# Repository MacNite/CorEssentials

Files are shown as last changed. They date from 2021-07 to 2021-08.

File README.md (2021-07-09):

# CorEssentials MK1
CorEssentials is an open source corexy 3D printer. This printer combines the best of the most popular 3D printers:

Voron V1.8 / V2.4 by VoronDesign: https://vorondesign.com/

HevoRT https://hevort.com/

Railcore https://railcore.org/

VZBot https://grabcad.com/library/vzbot-1

# supported by https://www.cr-3d.de

- Built Volume: 310 mm x 310 x mm x 310 mm
- Frame: Built from 2040, 2020 and 3030 Aluminium Extrusion
- Hotend: Trianglelab Dragon (0.4mm)
- Extruder: CR3D NanoXtruder
- Bed Leveling: Hardware bed leveling with 2 independent motors
- Built Plate: Magnetic Spring Steel with PEI or Pertinax
- Heated Bed: 230V, 800W silicone heater up to 120°C
- Connectivity: 7" Touchscreen, Wifi
- Filament runout sensor (Prusa Mini)
- Enclosure: Completely enclosed print volume with active temperature regulation and passive heated chamber (through heated bed)
- LED illumination
- Open for all Filament
- Filament Diameter: 1.75mm
- Supported Filament: ABS, ASA, PC, Nylon, PETG, PLA, PP, HIPS and much more // carbon and particle filled filaments possible with different toolhead
- Controller: Duet Mini 5+
- Power Supply: Meanwell 24V 10A, second PSU for High Voltage Stepper Drivers possible
- Coldend cooling: 3010 axial fan
- Part cooling: 1x 4020 blower fan
- Chamber fan & filtration: 6010 blower fan
- Electronics cooling: 2x 6015 axial fan
- Linear Motion: CE MGN9H for xy gantry and 8mm rods for z
- Completely open source: all Fusion 360 files and .stp assembly available

Find the Fusion360 model for your viewing/download pleasure here (you can download the F360 model through this link as well):

https://a360.co/3fYgmHP

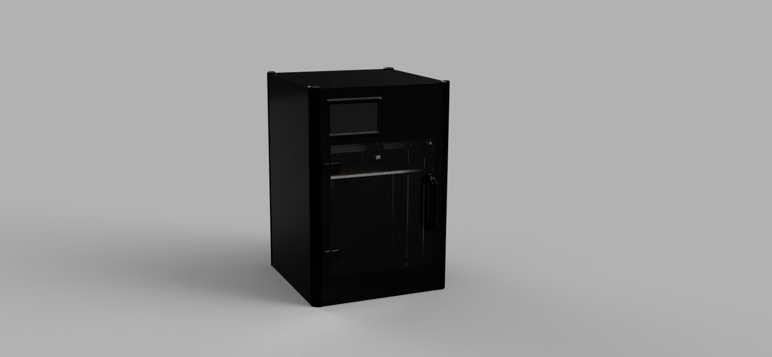
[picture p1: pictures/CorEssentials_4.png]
CorEssentials MK1


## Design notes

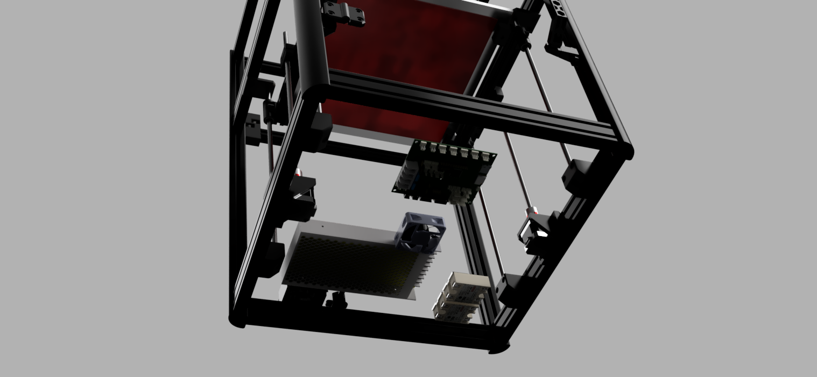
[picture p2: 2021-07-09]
pictures/CorEssentials_3.png

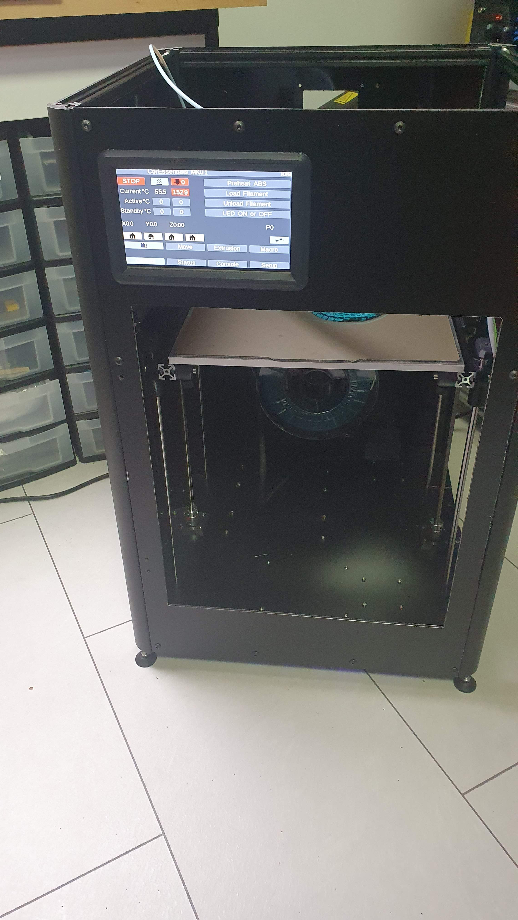
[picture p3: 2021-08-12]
pictures/CorEssentials_MK01_Foto1.jpg

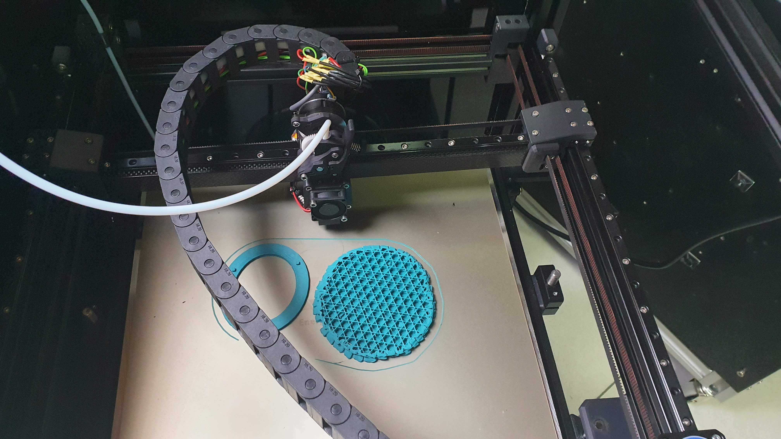
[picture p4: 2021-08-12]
pictures/CorEssentials_MK01_Foto3.jpg

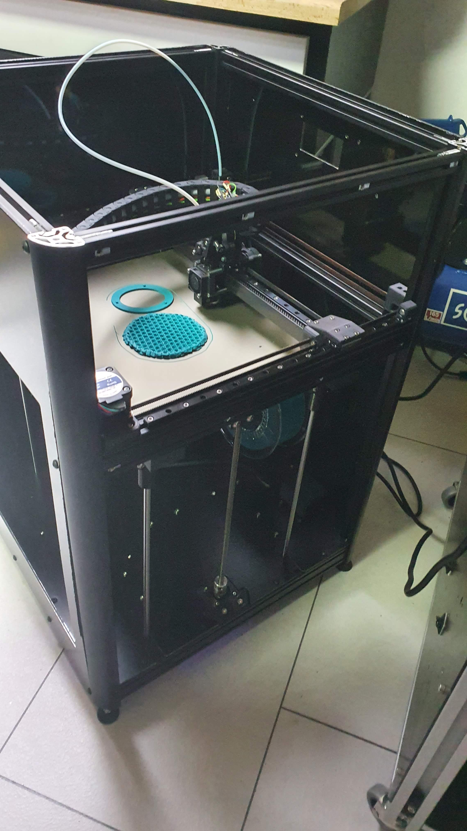
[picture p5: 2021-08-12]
pictures/CorEssentials_MK01_Foto2.jpg

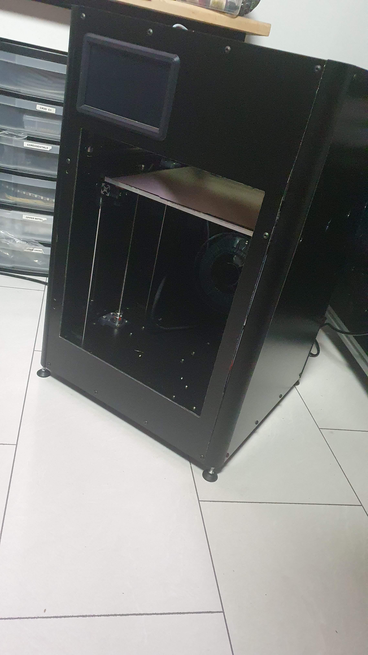
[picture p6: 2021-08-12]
pictures/CorEssentials_MK01_Foto4.jpg

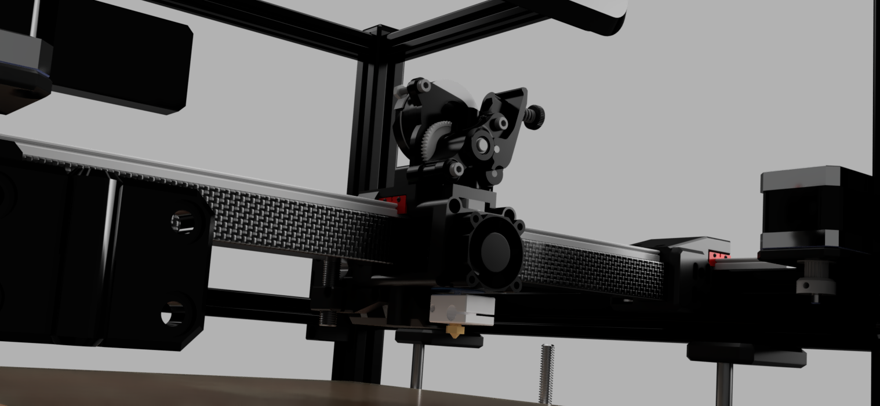
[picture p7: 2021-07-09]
pictures/CorEssentials_2.png

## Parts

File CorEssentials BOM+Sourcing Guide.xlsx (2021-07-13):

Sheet: Configurator
Configurator
Attention: The files for the panels are only available for the standard 310 x 310 x 310 mm³ built volume. If you plan to built any other size you have to edit the panels yourself.
Fields with this colour are input fields
Fields with this colour are name / title fields
Filds with this colour have formulas in them
Built Volume
Travel in x | 310 | mm
Travel in y | 310 | mm
Travel in z | 310 | mm
Fully enclosed? | yes
Corner Connection? | automatic connectors (more expensive but cleaner)
Needed Aluminium Profiles
Profile | Length |  | Amount needed | Used for
2020 | 410 | mm | 2 | Frame x
2020 | 420 | mm | 2 | Frame y
2020 | 351 | mm | 1 | Frame Back
4020 | 410 | mm | 2 | Frame x
4020 | 420 | mm | 4 | Frame y
3030 | 681 | mm | 4 | Frame z
2020 | 284 | mm | 2 | Bed Carrier
Carbon 20x20 |  | mm | 1 | x-Axis
Needed Linear Motion Components
Type | Length |  | Amount needed | Used for
8mm Rod | 404 | mm | 4 | z Axis
TR8x1,5 | 365 | mm | 2 | z Axis
MGN9H | 350 | mm | 1 | x Axis
MGN9H | 350 | mm | 2 | y-Axis
Built Plate
Component | Length |  | Amount needed | Used for
Bed Plate t = 8mm | 320 | mm | 1 | x-Length
 | 320 | mm |  | y-Length
Silicone Heater | 280 | mm | 1 | x-Length
 | 280 | mm |  | y-Length
Springsteel Sheet | 310 | mm | 1 | x-Length
 | 310 | mm |  | y-Length
Panels for enlcosure
Component | Length |  | Amount needed | Used for
Front + Back | 410 | mm | 2 | x-Length
 | 681 | mm |  | z-Length
Left+Right | 420 | mm | 2 | y-Length
 | 681 | mm |  | z-Length
Inner, Top, Bottom | 460 | mm | 3 | x-Length
 | 470 | mm |  | y-Length

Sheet: CorEssentials BOM
Category | Component | QTY | approx. Price | Source (partially affiliate links) | Note / Alternative Source
Filament | ABS Filament, 1kg | 1 | 25.00 €
Frame | 2020, L= 410mm | 2 | 135.00 € | https://www.myaluprofil.de/advanced_search_result.php?categories_id=0&inc_subcat=1 | Frame x
Frame | 2020, L= 420mm | 2 |  |  | Frame y
Frame | 2020, L= 351mm | 1 |  |  | Frame Back
Frame | 4020, L= 410mm | 2 |  | https://www.myaluprofil.de/Aluminiumprofil-20x40-Nut-5--I-Typ-.html | Frame x
Frame | 4020, L= 420mm | 4 |  |  | Frame y
Frame | 3030, L= 681mm | 4 |  | https://www.myaluprofil.de/Aluminiumprofil-R30x90---Nut-6--I-Typ-leicht-.html | Frame z
Frame | 2020, L= 284mm | 2 |  | https://www.myaluprofil.de/advanced_search_result.php?categories_id=0&inc_subcat=1 | Bed Carrier
Frame | Carbon 20x20, L= mm | 1 | 18.00 € | https://s.click.aliexpress.com/e/_AAvO8Y | 20x20x18
Frame | Automatic Connector | 50 | 82.00 € | https://www.myaluprofil.de/gewinde-formverbindersatz-nut-5-i-typ.html
Fasteners | M5 Thumbscrews for Bed | 4 | 4.00 € | https://s.click.aliexpress.com/e/_AW3sgC
Fasteners | M3 Nyloc Nut | 25 | 2.00 € | https://s.click.aliexpress.com/e/_AEa5uM
Fasteners | M4 Nyloc Nut | 4 | 100.00 €
Fasteners | BHCS M3x20 | 4
Fasteners | BHCS M3x30 | 4
Fasteners | BHCS M3x35 | 4
Fasteners | BHCS M3x40 | 4
Fasteners | BHCS M4x6 | 8
Fasteners | BHCS M4x14 | 4
Fasteners | BHCS M5x8 Black | 83
Fasteners | BHCS M5x10 | 9
Fasteners | BHCS M5x12 | 6
Fasteners | BHCS M5x20 | 10
Fasteners | BHCS M5x25 | 3
Fasteners | BHCS M5x35 | 2
Fasteners | SHCS M2.5x8 | 4
Fasteners | SHCS M3x8 | 29
Fasteners | SHCS M3x10 | 12
Fasteners | SHCS M3x12 | 4
Fasteners | SHCS M3x16 | 1
Fasteners | SHCS M3x18 | 3
Fasteners | SHCS M3x20 | 10
Fasteners | SHCS M3x25 | 5
Fasteners | SHCS M3x35 | 3
Fasteners | SHCS M3x50 | 2
Fasteners | SHCS M5x30 | 6
Fasteners | T-Slot Nut, Slot 5, M3 | 11
Fasteners | T-Slot Nut, Slot 5, M5 | 106
Fasteners | T-Slot Nut, Slot 6, M4 | 50
Fasteners | T-Slot Nut, Slot 6, M5 | 9
Fasteners | Countersunk M3x8 | 8
Fasteners | Countersunk M5x25 | 4 |  |  | Bed
Motion | 8mm Rod, L= 404mm | 4 | 16.00 € | https://de.aliexpress.com/item/32676553191.html | z Axis
Motion | TR8x1,5, L= 365mm | 2 | 12.00 € | https://www.motedis.com/shop/Dynamik/Trapezgewindespindel-Zubehoer/Trapezgewindespindel-RPTS-rechts-TR-16x4-L%3D1000mm::4800.html | z Axis
Motion | MGN9H, L= 350mm | 1 | 14.00 € | https://de.aliexpress.com/item/33043386369.html?spm=2114.13010708.0.0.9a244c4dHEINjY | x Axis
Motion | MGN9H, L= 350mm | 2 | 28.00 € | https://de.aliexpress.com/item/33043386369.html?spm=2114.13010708.0.0.9a244c4dHEINjY | y-Axis
Motion | Coupling 8x5mm - Leadscrew to stepper | 2 | 15.00 € | https://de.aliexpress.com/item/32673106538.html?spm=2114.13010708.0.0.14d84c4dMCanQh
Motion | TR8x1,5 Leadscrew Nut (IGUS) | 1 | 8.00 € | https://www.motedis.com/shop/Dynamik/Trapezgewindespindel-Zubehoer/Standard-Anti-backlash-Delrin-Mutter-TR-8x15::3955.html
Motion | GT2 6mm Belt, 4m | 1 | 18.00 € | https://s.click.aliexpress.com/e/_AEHEpa
Motion | GT2 16T Idler - Smooth / no teeth - Bore 3mm | 2 | 6.00 € | https://s.click.aliexpress.com/e/_A8v4QU
Motion | GT2 16T Idler - with teeth - Bore 3mm | 6 | 16.00 € | https://s.click.aliexpress.com/e/_A8v4QU
Motion | GT2 20T Pulley - Bore 5mm | 2 | 5.00 € | https://s.click.aliexpress.com/e/_Aerhni
Motion | LM8UU | 8 | 7.00 € | https://de.aliexpress.com/item/32227295989.html
Electronics | Triangelalab Dragon Hotend (High Flow) | 1 | 70.00 € | https://s.click.aliexpress.com/e/_AFV3Is
Electronics | Trianglelab 50Watt Heater Cartridge, 24V | 1 | 3.00 € | https://s.click.aliexpress.com/e/_A3MKFA
Electronics | Termistor 104GT-2 104 NT | 2 | 8.00 € | https://s.click.aliexpress.com/e/_Alchb2
Electronics | Prusa Mini Filament Sensor Electronics | 1 | 8.00 € | https://s.click.aliexpress.com/e/_AXDKUC
Electronics | 3010 axial fan, Dual Ball Bearing, 24V | 1 | 11.00 € | https://s.click.aliexpress.com/e/_9jQWYg
Electronics | 6010 axial fan, Dual Ball Bearing, 24V | 2 | 9.00 € | https://s.click.aliexpress.com/e/_AK0dze
Electronics | 6015 Blower Fan, Dual Ball Bearing, 24V | 1 | 8.00 € | https://s.click.aliexpress.com/e/_9HHvkM
Electronics | 4020 blower fan, Dual Ball Bearing, 24V | 1 | 9.00 € | https://s.click.aliexpress.com/e/_9GZzKu
Electronics | Fysetc PanleDue 7i | 1 | 50.00 € | https://s.click.aliexpress.com/e/_AfTH3w
Electronics | Fysetc Duet 3 Mini 5+ Wifi | 1 | 55.00 € | https://s.click.aliexpress.com/e/_9QsNAY | https://www.cr3d.de/produkt/duet-3-mini-5/
Electronics | CR3D SupCRprobe 8mm kurz (Alternative: Prusa SuperPinda) | 1 | 25.00 € | https://www.cr3d.de/produkt/supcrprobe-8mm-kurz/
Electronics | Wifi Antenna cable extension (SMA Female 100cm) | 1 | 3.00 € | https://s.click.aliexpress.com/e/_9w3PT2
Electronics | Nema 17 (Body L<40mm), 17HS19-2004S1 | 4 | 40.00 € | https://s.click.aliexpress.com/e/_9yAVtA
Electronics | SSR for Heated Bed (current rating at least 10A AC) | 1 | 30.00 € | https://www.cr3d.de/produkt/solid-state-relais-10a/
Electronics | Thermal Fuse for Heated Bed, 125°C | 1 | 3.00 € | https://s.click.aliexpress.com/e/_9Ah1FE
Electronics | IEC Socket with fuse and switch (Type AC-17) | 1 | 5.00 € | https://s.click.aliexpress.com/e/_Apvyuo
Bed | Bed Plate t = 8mm, 320x320mm | 1 | 42.00 € | https://www.metall-kunststoffhandel.de/produkt/aluminium-al-mg-45-mn-8-mm-feinstgefraest/
Bed | Silicone Heater, 280x280mm | 1 | 20.00 € | https://s.click.aliexpress.com/e/_ArIUe8
Bed | Springsteel Sheet, 310x310mm | 1 | 37.00 € | https://s.click.aliexpress.com/e/_9HHdEY
Other | CR3D NanoXTruder (Alternative: Print parts on your own and buy Orbiter) | 1 | 70.00 € | https://www.cr3d.de/produkt/cr-3d-nanoxtruder/ | https://de.aliexpress.com/item/1005002487727392.html?spm=2114.13010708.0.0.3a994c4dKlcmqN
Other | Front + Back, 410x681mm, thickness: 3 to 4 mm | 2 | 150.00 € | https://kunststoffplattenonline.de/product/alupanel-alu-verbundplatten-schwarz-3-mm/ | a) can be cnc / cut with hand tools from aluminium composite panel b) can be hand cut (knife) from PVC foam or similar c) can be ordered form laser-cutting services in 3mm aluminium
Other | Left+Right, 420x681mm, thickness: 3 to 4 mm | 2
Other | Inner, Top, Bottom, 460x470mm, thickness: 3 to 4 mm | 3
Other | Filter for Enclosure | 1 | 5.00 € | https://s.click.aliexpress.com/e/_ABCy64
Sum |  |  | 1172.00 €

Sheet: Fusion360_BOM_Import
Parts List
Qty | Part Number | ITEM Slot 6 Nut M4
 |  | 0
1 | AC_Power_Socket-3_pin_250V_10A_AC-17
1 | Case_PC
2 | Êîíòàêò
1 | Êîíòàêò_GND
3 | Êëåéìà
1 | Fuse_contact
1 | Êîíòàêò_fuse
1 | Fuse_holder
1 | Fuse_contact (1)
1 | Êîíòàêò_fuse
1 | Fuse_holder
1 | Ïåðåìû÷êà
1 | SWITCH KCD1-104_Default<As Machined>
1 | Äåðæàòåëü_ïðåäîõðàíèòåëÿ_ñ_ïðåäîõðàíèòåëåì
1 | Äåðæàòåëü_ïðåäîõðàíèòåëÿ
1 | Fuse Small 1A
3 | CornerConnector
1 | M5 Threaded Insert
1 | 92095A208_Button Head Hex Drive Screw
1 | IEC_Cover
1 | Chamber_Fan_Cover
2 | 60mm Fan
1 | Fan_Case
1 | Fan
2 | Meanwell LRS-200-24
1 | Duet3_5+_Wifi
1 | USB_Micro-B_Molex_47346-0001
1 | SOLID
1 | IDC-Header_2x13_P2.54mm_Vertical
1 | SOLID (5)
1 | 9.5mm_1x4
1 | SOLID (7)
7 | Molex_KK-254_AE-6410-02A_1x02_P2.54mm_Vertical
1 | SOLID (11)
3 | IDC-Header_2x05_P2.54mm_Vertical
1 | SOLID (13)
1 | 693071020811_Download_STEP_693071020811_rev1
1 | COMPOUND (1)
1 | ESP-WROOM-02U
1 | SOLID (15)
3 | PinHeader_1x03_P2.54mm_Vertical
1 | SOLID (17)
5 | Molex_KK-254_AE-6410-03A_1x03_P2.54mm_Vertical
1 | SOLID (20)
1 | PinHeader_1x16_P2.54mm_Vertical
1 | SOLID (21)
7 | Molex_KK-254_AE-6410-04A_1x04_P2.54mm_Vertical
1 | SOLID (25)
1 | PinHeader_2x05_P2.54mm_Vertical
1 | SOLID (27)
1 | TQFP-128_14x14mm_P0.4mm
1 | SOLID (30)
1 | C-K_Components_Switch_Tactile_KMS
1 | COMPOUND (4)
1 | PinHeader_1x02_P2.54mm_Vertical
1 | SOLID (38)
5 | Molex_KK-254_AE-6410-05A_1x05_P2.54mm_Vertical
1 | SOLID (39)
2 | B2P-VH-B-white
1 | SOLID (40)
2 | Mini_Blade_Fuse_Holder
1 | COMPOUND (5)
2 | Fuse_MINI
1 | COMPOUND (6)
1 | COMPOUND (7)
4 | DoorHinge
1 | DoorHandle
1 | Door_Lock_C
2 | Door_Lock_A
1 | 92095A210_Button Head Hex Drive Screw
1 | Door_Lock_B
1 | DasFilament_Standard
1 | Prusa_Mini FilamentSensor
1 | MINI-fsenzor-lever
1 | MINI-fsenzor-cover
1 | MINI-fsenzor-box
1 | 90751A113
1 | 92095A214_Button Head Hex Drive Screw
1 | 90128A205
1 | 91274A103
1 | Spool_Holder
1 | Bowden_Tube_Clip
8 | Magnet_6x3mm
10 | M3 Threaded Insert
1 | 91290A123
2 | M5 Threaded Insert
1 | 91263A823
1 | 92095A208_Button Head Hex Drive Screw
1 | 91502A104
1 | 91290A121
4 | Stellfuss
2 | _sASM zStage
1 | Axialkugellager F5-10
1 | Motor Nema 17 US-17HS4401 v4
1 | Wellenkupplung 5x8
1 | Leadscrew Nut TR8x1,5
1 | TR8x1,5 L=365mm
2 | Z_Rod_Mount_Bottom
1 | 97763A433
1 | 92095A220_Button Head Hex Drive Screw
2 | Z_Rod_Mount_Top
1 | 92095A214_Button Head Hex Drive Screw
4 | Lm8uu
2 | Z_Bearing_Holder
1 | 92095A214_Button Head Hex Drive Screw
1 | Z_Leadscrew_Spacer
1 | 2020 L=284mm_Bed
2 | BedCarrier
1 | M5 Knurled Nut
1 | 97763A433
1 | 92095A214_Button Head Hex Drive Screw
1 | 92095A208_Button Head Hex Drive Screw
1 | 92095A210_Button Head Hex Drive Screw
1 | 91502A104
1 | _sASM XY_Stage
3 | MGN9H 350mm Assembly
1 | MGNR9_L350
1 | 91274A103
1 | MGN9H
2 | 2040 L=420mm_Frame_y
2 | Motor Nema 17 US-17HS4401 v4
2 | GT2 20T
1 | GT2 M8
8 | GT2 16T Idler
1 | X-Brace
1 | Xy_Joiner_Left
1 | Xy_Joiner_Left(Mirror)
2 | Xy joiner spacer
1 | X-carriage
2 | Belt-Tensioner
2 | X-Belt-Clamp
1 | 91274A103
1 | Tool_Cartridge
1 | 3010fan
1 | Component1
1 | 4020TB
1 | 4020p1
1 | 4020p3
1 | 4020p2
1 | Extruder_Mount
1 | X-Brace_Retainer
2 | Xy-Steper_mount
1 | 91263A823
1 | 91502A104
2 | Xy-Idler-Mount
1 | Y-Axis-Stopper (1)
2 | M5 Threaded Insert
1 | 2020 L=351mm_Frame_x_back
1 | Fanduct
2 | Blower_Spacer
1 | Probe_SupCR
1 | Inductive_Probe_Holder
1 | Dragon hotend
1 | CR3D NanoXtruder v3
1 | C1mini_Toolhead_NanoXtruder
1 | C1-Mini x-Achse mit Tool2
1 | C1-Mini x-Achse mit Tool3_Phaetus_Mount
1 | Fan_RLF35-8_14N_ebm-papst_RLF35-8_14N_ebm-papst
1 | Fan-House_RLF35-8_14N_ebm-papst_RLF35-8_14N_ebm-papst
1 | 40x40x10 DC Fan v1
1 | PINDA_placeholder v1
1 | PINDA_placeholder v1-1
1 | PINDA_placeholder v1-2
1 | C1mini_BeltClamp_X-Achse_hinten
1 | Fanduct_V2
1 | Endschalter_Cherry_DB2_mit_Hebel_mit_Zusatzbet㳩ger
1 | NanoXtruder_Abdeckung
1 | NanoXtruder_R�latte
1 | KHK_US-DS0_5-50
1 | Shaft
1 | RollerBearing
1 | IdlerShaft
1 | RollerBearing (1)
1 | IdlerGear
1 | Drive_Gear
1 | Thumbscrew
1 | Washer
1 | Spring
1 | T10 SpurGear
1 | LDO_Stepper
1 | LDO_Stepper (1)
1 | LDO_Stepper (6)
1 | LDO_Stepper (11)
1 | LDO_Stepper (8)
1 | LDO_Stepper (9)
1 | LDO_Stepper (3)
1 | LDO_Stepper (10)
1 | LDO_Stepper (4)
1 | LDO_Stepper (2)
1 | LDO_Stepper (5)
1 | LDO_Stepper (7)
1 | LDO_Stepper (12)
1 | LDO_Stepper (15)
1 | LDO_Stepper (13)
1 | LDO_Stepper (14)
2 | Bearing_MR95_7804K105
2 | Bearing_MR95_7804K105-1
2 | Bearing_MR95_7804K105-2
2 | Bearing_MR95_7804K105-3
1 | M3_Nut_94150A325 v4
1 | M3_Nut_94150A325 v4 (1)
1 | TensionArm_Pin
1 | NanoXtruder_Hebel
1 | NanoXtruder_Body
1 | BMO
9 | M3 Nyloc Nut
1 | 90576A102_MEDIUM-STRENGTH STEEL NYLON-INSERT LOCKNUT
23 | M3 Threaded Insert
1 | 91274A103
1 | 92095A187_Button Head Hex Drive Screw
1 | 92095A201_Button Head Hex Drive Screw
1 | 90751A113
1 | 91290A123
1 | 90128A205
1 | 91502A112
1 | 91290A121
1 | 91502A114
1 | 95263A158
1 | 91502A104
1 | 90128A184
1 | 91290A194
1 | BuiltPLate
 |  | 0

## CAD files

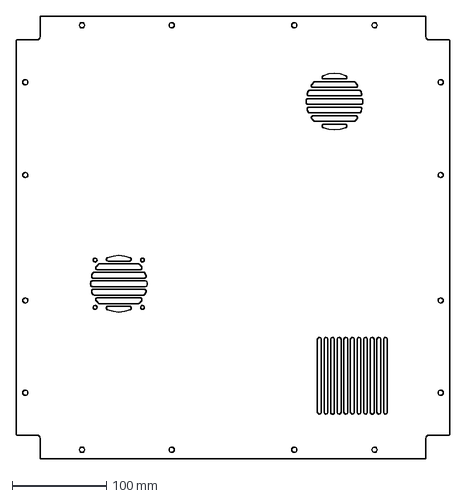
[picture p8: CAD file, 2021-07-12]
DXF/Panel_Bottom_x1.dxf
459.0 x 469.0 mm

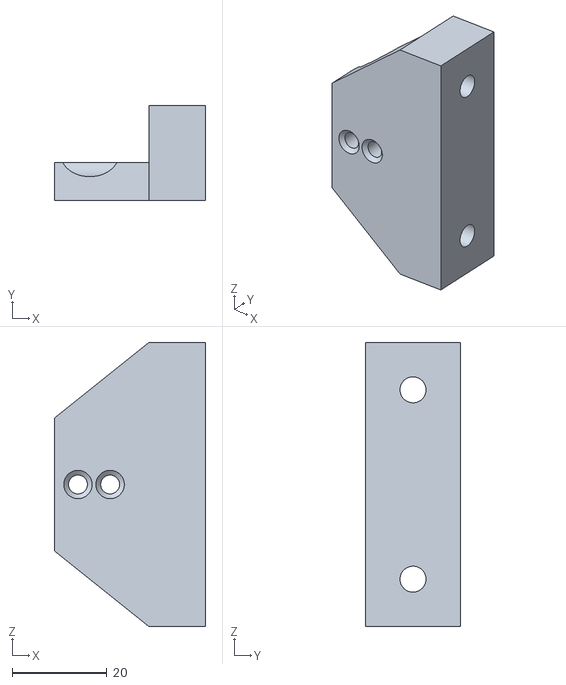
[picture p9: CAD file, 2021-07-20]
STL/Dragchain_Mount_Frame_x1.stl
32.0 x 20.0 x 60.0

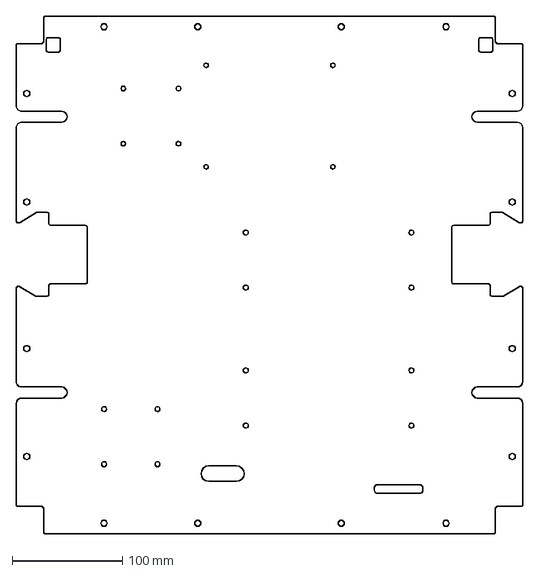
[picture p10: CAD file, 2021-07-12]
DXF/Panel_Inner_x1.dxf
459.0 x 469.0 mm

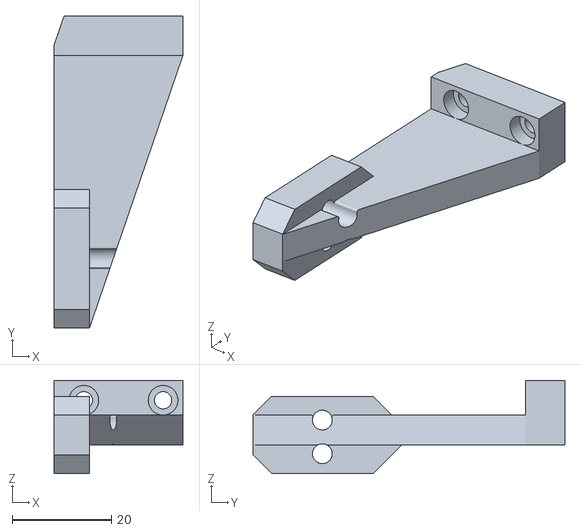
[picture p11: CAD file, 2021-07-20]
STL/X_Carriage_Dragchain_Mount_x1.stl
26.0 x 63.0 x 18.8

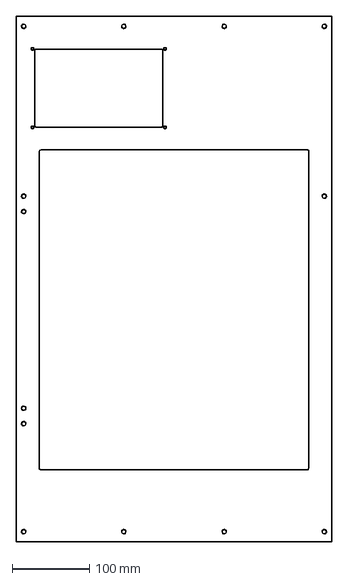
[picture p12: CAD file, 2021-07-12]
DXF/Panel_Front_x1.dxf
409.4 x 681.0 mm

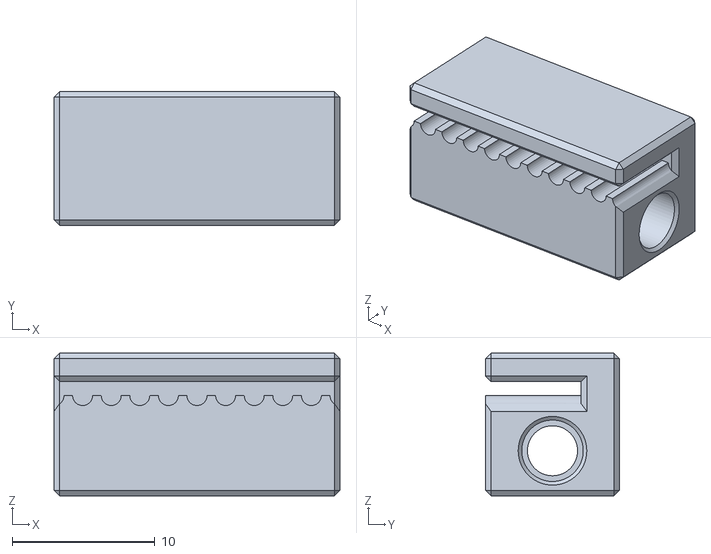
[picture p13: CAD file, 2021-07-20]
STL/Belt_Tensioner_x2.stl
20.0 x 9.40 x 10.00

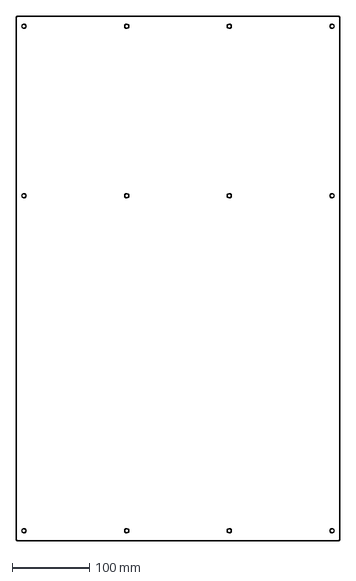
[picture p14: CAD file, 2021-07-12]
DXF/Panel_Side_x2.dxf
419.4 x 681.0 mm

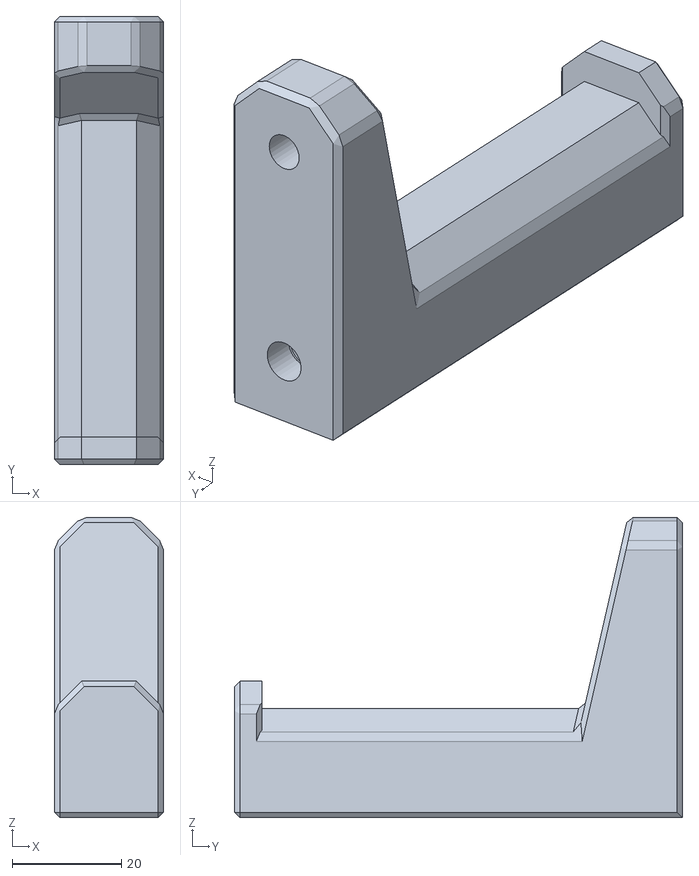
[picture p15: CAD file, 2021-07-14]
STL/Spool_Holder_x1.stl
20.0 x 82.0 x 55.0

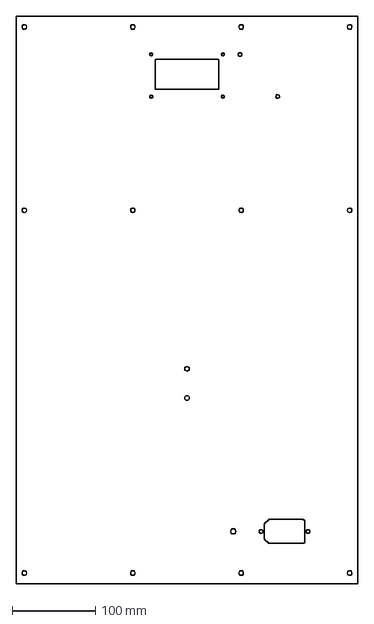
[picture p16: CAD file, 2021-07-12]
DXF/Panel_Back_x1.dxf
409.4 x 681.0 mm

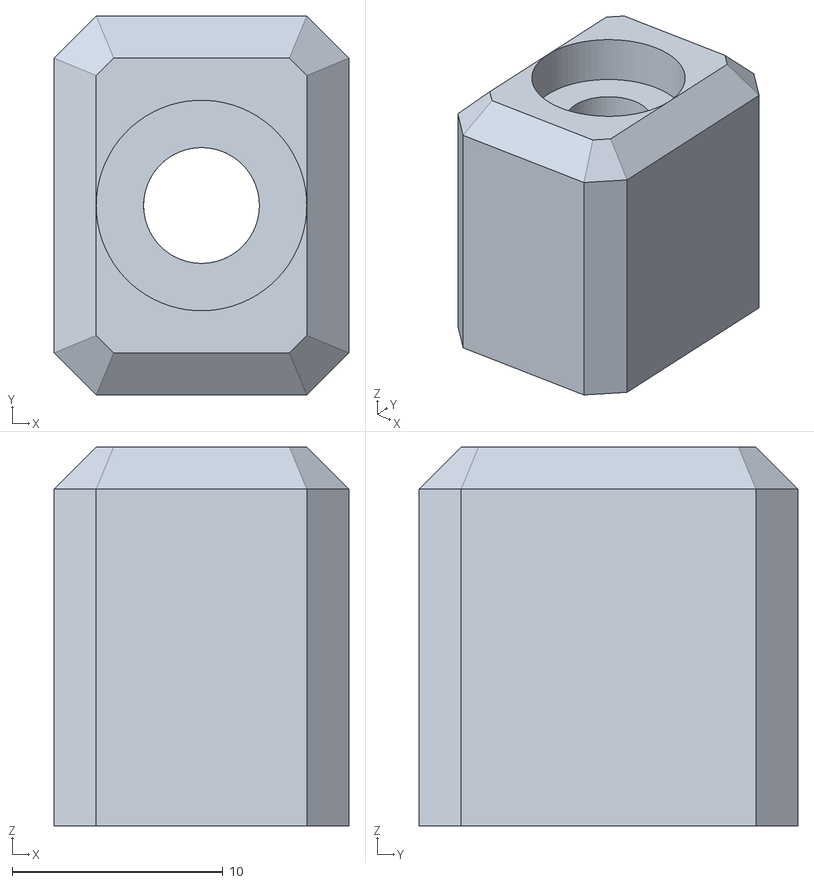
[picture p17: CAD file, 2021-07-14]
STL/y_Axis_Stopper_x2.stl
14.0 x 18.0 x 18.0

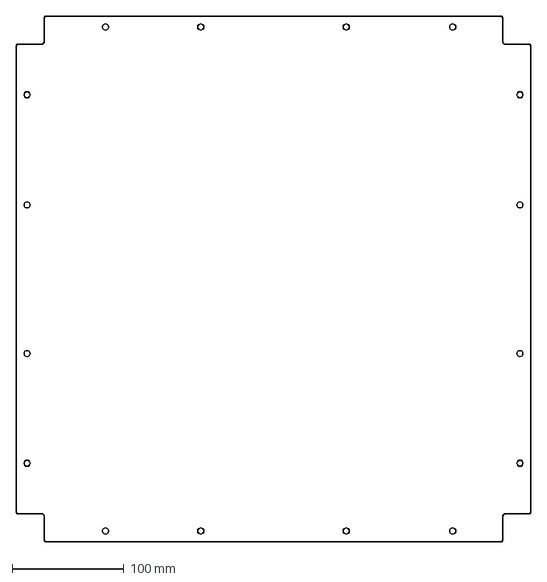
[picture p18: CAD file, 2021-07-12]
DXF/Panel_Top_x1.dxf
459.0 x 469.0 mm

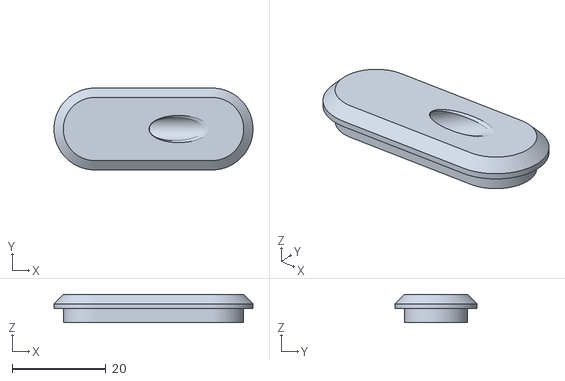
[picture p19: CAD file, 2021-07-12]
STL/Bed_Cable_Passthrough_x1.stl
42.5 x 17.5 x 6.00

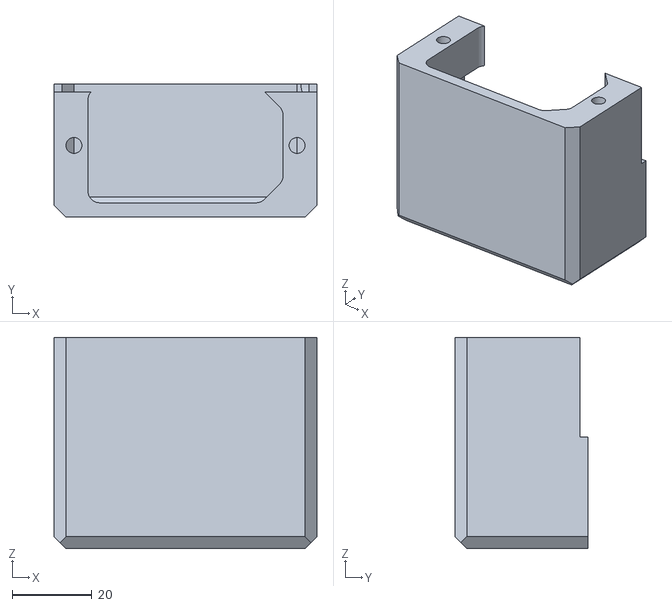
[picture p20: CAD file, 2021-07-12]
STL/IEC_Cover_x1.stl
66.0 x 33.5 x 53.0

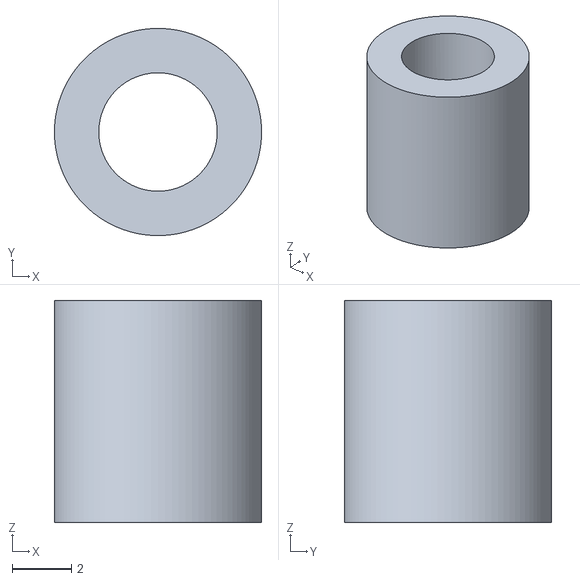
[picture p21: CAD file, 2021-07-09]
STL/X_Carriage_FanSpacer_x2.stl
7.00 x 7.00 x 7.50

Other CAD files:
STL/Enclosure_Fan_Cover_x1.stl
STL/Belt_Clamp_x2.stl
STL/Extrusion_Cover_x4.stl
STL/XY_Joiner_Cover_Left_x1.stl
STL/Corner_Connector_x3.stl
STL/Door_Handle_x1.stl
STL/Door_Hinge_x4.stl
STL/Door_Lock_A_x2.stl
STL/Door_Lock_B_x1.stl
STL/Door_Lock_C_x1.stl
STL/DuetMini5+_Fanduct_x1.stl
STL/Extruder-Backplate_x1.stl
STL/Extruder_Body_x1.stl
STL/Extruder_Cover_x1.stl
STL/Extruder_Lever_x1.stl
STL/Extruder_Mount_x1.stl
STL/Filament_Sensor_Body_x1.stl
STL/Filament_Sensor_Cover_x1.stl
STL/Filament_Sensor_Lever_x1.stl
STL/Filament_Sensor_Mount_x1.stl
STL/Filter_Mount_x1.stl
STL/Inductive_Probe_Mount_x1.stl
STL/LCD_Bezel.stl
STL/LCD_Spacer.stl
STL/PTFE_Tube_holder_x1.stl
STL/Tool_Cartridge_Dragon_x1.stl
STL/Tool_Cartridge_V6_x1.stl
STL/XY_Idler_x2.stl
STL/XY_Joiner_Cover_Right_x1.stl
STL/XY_Joiner_Left_x1.stl
STL/XY_Joiner_Right_x1.stl
STL/XY_Stepper_Mount_x2.stl
STL/X_Carriage_Fanduct_x1.stl
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

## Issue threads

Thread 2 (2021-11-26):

Meshbed not working

sanczess, 2021-11-26:
Meshbed compensation not working correctly.
The compensation either overcompensates or inverts the hightmap.
Mechanical issues in that device already solved, but maybe there are more of them hidden.
Printhead is tilting on rail which maybe is a further issue.
Printplate is damaged totaly already because of that issue.
No printing in full area possible

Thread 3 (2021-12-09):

Cable breake

sanczess, 2021-12-09:
The design of cable guidance is horrible. The printer worked for 6 months, now extruder cables broke twice within one week.
**MacNite is unable to design 3D Printers.**
There were many mechanical Issues with this device.
**All people** who are interested in MacNites machines: **You are warned by me!!!!**
This man doesnt know what he makes

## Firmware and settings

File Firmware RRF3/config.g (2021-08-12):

; Configuration file for Duet 3 Mini 5+ (firmware version 3)
; executed by the firmware on start-up
;
; generated by RepRapFirmware Configuration Tool v3.2.3 on Wed Jun 02 2021 13:51:01 GMT+0200 (Mitteleuropäische Sommerzeit)

; General preferences
G90                                                   ; send absolute coordinates...
M83                                                   ; ...but relative extruder moves
M550 P"CorEssentials MK0.1"                           ; set printer name
M669 K1                                               ; select CoreXY mode

; Network
M552 S1                                               ; enable network
M586 P0 S1                                            ; enable HTTP
M586 P1 S0                                            ; disable FTP
M586 P2 S0                                            ; disable Telnet
; Drives
M569 P0.0 S0                                          ; physical drive 0.0 goes backwards
M569 P0.1 S0                                          ; physical drive 0.1 goes backwards
M569 P0.2 S1                                          ; physical drive 0.2 goes forwards
M569 P0.3 S1                                          ; physical drive 0.3 goes forwards
M569 P0.4 S0                                          ; physical drive 0.4 goes backwards
M584 X0.0 Y0.1 Z0.2:0.3 E0.4                          ; set drive mapping
M350 X16 Y16 Z16 E16 I1                               ; configure microstepping with interpolation
M92 X80 Y80 Z2133.333333333333 E703          		  ; set steps per mm
M566 X1800 Y1800 Z60 E120                             ; set maximum instantaneous speed changes (mm/min)
M203 X60000 Y60000 Z300 E1200                         ; set maximum speeds (mm/min)
M201 X5000 Y5000 Z500 E1000                           ; set accelerations (mm/s^2)
M906 X1200 Y1200 Z1000 E700 I30                       ; set motor currents (mA) and motor idle factor in per cent
M84 S30                                               ; Set idle timeout

; Axis Limits
M208 X0 Y0 Z0 S1                                      ; set axis minima
M208 X310 Y310 Z310 S0                                ; set axis maxima
M671 X-33.5:377 Y155:155 S2                           ; position of leadscrews, maximum correction S=2mm

; Endstops
M574 X2 S3                                            ; configure sensorless endstop on X
M574 Y2 S3                                            ; configure sensorless endstop on Y
M574 Z1 S2                                            ; configure z-probe endstop for low end on Z

; Sensorless Homing Limits
M915 X Y S8 F0 H200 R0                                ; S: Stall detection threshold; recommended values -10 to +63 / F: Filter Mode: 0 = unfiltered, every full step

; Z-Probe
M558 P5 C"^io3.in" H5 F120 T18000                     ; set Z probe type to switch and the dive height + speeds
G31 P500 X-24 Y59 Z1.8                              ; set Z probe trigger value, offset and trigger height
M557 X30:270 Y60:270 P5                               ; define mesh grid, P: 5 points in x- and y-direction

; Heaters & Sensors
M308 S0 P"temp0" Y"thermistor" T100000 B4092          ; configure sensor 0 as thermistor on pin temp1
M950 H0 C"out0" T0                                    ; create bed heater output on out1 and map it to sensor 0
M307 H0 B0 S1.00                                      ; disable bang-bang mode for the bed heater and set PWM limit
M140 H0                                               ; map heated bed to heater 0
M143 H0 S115                                          ; set temperature limit for heater 0 to 115C
M308 S1 P"temp1" Y"thermistor" T100000 B4725 C7.06e-8 ; configure sensor 1 as thermistor on pin temp0
M950 H1 C"out1" T1                                    ; create nozzle heater output on out0 and map it to sensor 1
M307 H1 B0 S1.00                                      ; disable bang-bang mode for heater  and set PWM limit
M143 H1 S315                                          ; set temperature limit for heater 1 to 315C
M308 S2 P"temp2" Y"thermistor" T100000 B4725 C7.06e-8 A"Chamber" ; configure sensor 2 as thermistor on pin temp2

; Fans
M950 F0 C"out3" Q500                                  ; create fan 0 on pin out3 and set its frequency
M106 P0 C"Coldend" S1 H1 T45                          ; set fan 0 name and value. Thermostatic control is turned on
M950 F1 C"out4" Q500                                  ; create fan 1 on pin out4 and set its frequency
M106 P1 C"Part" S0 H-1                                ; set fan 1 name and value. Thermostatic control is turned off
M950 F2 C"out2" Q500                                  ; create fan 2 on pin out5 and set its frequency
M106 P2 C"Chamber" S0 H2 T45                          ; set fan 2 name and value. Thermostatic control is turned off

; Filament Runout Sensor
M591 D0 P1 C"io2.in" S1

; Tools
M563 P0 S"Dragon" D0 H1 F0:1                          ; define tool 0
G10 P0 X0 Y0 Z0                                       ; set tool 0 axis offsets
G10 P0 R0 S0                                          ; set initial tool 0 active and standby temperatures to 0C

; Pressure advance
;M572 D0 S0.03                                        ; Direct Drive: S0.025 - Short Bowden (200mm): S0.1

; Custom settings are not defined

; Miscellaneous
M575 P1 S1 B57600                                     ; enable support for PanelDue
M501                                                  ; load saved parameters from non-volatile memory
T0                                                    ; select first tool

; LED
M150 X1 Q3000000                                      ; set LED type to NeoPixel and set SPI frequency to 3MHz
M150 R255 U255 B255 P255 S21						  ; turn all LED on White
global LED_state=true								  ; set variable for LED on

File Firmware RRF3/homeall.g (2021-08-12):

; homeall.g
; called to home all axes

	;	 homex
M569 P0.0 V50    ; make sure x-drive stays in stealthChop Mode
G91               ; relative positioning
G1 H2 Z5 F1800   ; lift Z relative to current position

;stealthChop calibration
G1 H1 X0.5 F1000  ; move 2 micro steps away from endstop
G4 P200           ; wait 100ms
G1 H1 X5 F1000    ; move 5mm away from homing direction
G4 P200           ; wait 100ms
M400              ; wait for all moves to finish
M913 X50          ; set current of x-stepper to 50%
;Homing move
G1 H1 X315 F6000 	; move quickly to X axis endstop and stop there (first pass)
G1 X-5 F18000      	; go back a few mm
G1 H1 X315 F6000 	; move slowly to X axis endstop once more (second pass)
G90               	; absolute positioning
; set standard settings
M913 X100         ; set current of x-stepper to 100%
M569 P0.0 V2000   ; stealthChop Mode only for slow moves


	; 	homey
M569 P0.1 V50    ; make sure y-drive stays in stealthChop Mode
G91               ; relative positioning
;stealthChop calibration
G1 H1 Y-0.5 F1000 ; move 2 micro steps away from endstop
G4 P200           ; wait 100ms
G1 H1 Y-5 F1000   ; move 5mm away from homing direction
G4 P200           ; wait 100ms
M400              ; wait for all moves to finish
M913 Y50          ; set current of y-stepper to 50%
;Homing move
G1 H1 Y315 F6000 ; move quickly to X axis endstop and stop there (first pass)
G1 Y-5 F18000      ; go back a few mm
G1 H1 Y315 F6000 ; move slowly to X axis endstop once more (second pass)
G90               ; absolute positioning
; set standard settings
M913 Y100         ; set current of x-stepper to 100%
M569 P0.1 V2000   ; stealthChop Mode only for slow moves

	; 	home z

G1 X155 Y155 F12000 ; move to center of bed
M558 F6000    
G30
M558 F120
G30
G1 Z5 F600

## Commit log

2019-12-07 First Edition
    [CorEssentials BOM+Sourcing Guide.xlsx, Door.dxf, Plate_Back x1.dxf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]
2019-12-08 added files for different nozzle sizes
    [Nano_Tool_015_Support.stl, Nano_Tool_025_Support.stl, Nano_Tool_030_Support.stl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]
2020-01-14 Create STL
2020-01-14 Add files via upload
    Initial Release
    [Back_6mm.dxf, Bottom_Electronic_6mm.dxf, Door_5mm.dxf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]
2020-01-16 Update README.md
    - BOM update complete
2020-11-25 First Release
    3D printed Model:
    Adalinda: The Singing Serpent bei Loubie
    https://www.thingiverse.com/thing:246198
2020-11-25 Initial Release
    [CorEssentials MK1 BOM.xlsx, Door_Hinge_x2.stl, Dragchain_End_Fixed_x2.stl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]
2021-07-09 MK1 initial release
    [Belt_Clamp_x2.stl, Belt_Tensioner_x2.stl, Corner_Connector_x3.stl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]
2021-07-12 STL Update
    IEC Cover: Changes for fitment
    Belt Tensioner: Corrected Belt orientation
    [Belt_Tensioner_x2.stl, IEC_Cover_x1.stl]
2021-07-13 Add files via upload
    Add configurator:
    - select print volume
    - select if you want an enclosure ore not (BOM will be updated)
    - select which type of frame connector do you want: Blind or Automatic (BOM will be updated)
    [CorEssentials BOM+Sourcing Guide.xlsx]
2021-07-20 Add files via upload
    improved position and hole diameter of threaded insert for more easy assembly
    [Belt_Tensioner_x2.stl]
